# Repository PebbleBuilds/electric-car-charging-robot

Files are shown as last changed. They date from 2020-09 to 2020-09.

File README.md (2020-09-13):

# electric-car-charging-robot
This is a repo of files from an automatic electric car charging robot that I was designing with my friends Eddie Tian and Grace Wu before COVID19. This was done for a design course assignment with specific requirements, which are alluded to in our Project Proposal. 

For a summary of our plan, see Reports/Project Proposal.pdf. For a summary of the state of the robot as we left it before COVID19, see Reports/State of Robot as of March 2020.pdf. In the same file, there is also a list of the work breakdown between myself, Grace, and Eddie (I did not write all the files in this repo - I'm just uploading them here as a record of our work).

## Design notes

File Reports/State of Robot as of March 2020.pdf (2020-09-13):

Definitions:
The robot consists of three “stages” on which components are attached. The stage farthest from the test rig is the “x stage”, on the ground and closest to the test rig is the “y stage” and the highest stage is the “z stage.” Any components placed on these stages (such as motors and gears) will have a corresponding prefix. The end effector is attached to the z stage.

The lead screws which move the robot are named in the same fashion. The “x screw” is parallel to the test rig and the ground. The “y screw” is placed normal to the test rig. The “z screw” is parallel to the test rig and normal to the ground.

Our robot uses normal force carriers and platforms to transmit the rotational force of the gears into translational movement. When the gear turns and pushes the normal force carrier, it pushes the platform which is a block attached to the stage with an unthreaded screw which moves the stage in the desired direction. These components have the same prefix as the lead screw on which they move.

Robot Status
State of Mechanical
- Design of all mechanical components completed
- All components are finalized as of now except the following:
- The end effector has been assembled but not attached to the z stage.
- The camera mount has been assembled but not attached to the z stage.
- The top level of the robot the support rod holders attach to has been designed.
- The support rod holders has been designed.
- Motors have been placed in their respective mounts in the finalized position.
- Gears have been laser cut from acrylic and fitted to motors and lead screws.
- Movement along the x and y screws has been tested and functions on the ¾”-10 screws.
- X platform guard has been made to prevent wires from interfering with the x gears.
- Partial transition from ¾”-10 to ¾”-6 screws
- Note: due to supplier shortages, we were unable to use the lead screws specified in our design (¾”-6). Instead, we used ¾”-10 screws which we performed milestone 1 on
- After the milestone, we began to switch to ¾”-6 screws but still needs to be finished and tested.
Next steps:
- Finish transitioning to ¾”-6 screws.
- Laser cut the top level and support rod holders so support rods can be put in.
- Cut the polyethylene sheet to size so it can be attached to the z stage and slide along the support rods
- Test movement in the z direction
- Purchase standoffs to mount PCBs to stages
- Create guards around other moving parts to prevent harm to humans or wires.

- Determine if weight (sand or gravel) is required to weigh down the sides of the robot during operation.
Electrical
- Modular stepper motor driver circuits soldered (with pin headers for detaching/attaching drivers)
- Wire harness implemented for carrying power/signals between stages
- Circuits calibrated, debugged, and tested
Next steps:
- Add fan for active cooling, as well as 12V power from buck convertor for fan
- Design and purchase PCBs from Shenzhen to replace soldered perfboards, to increase current capacity and reliability (in time for Milestone 3)
- Remove excess solder from previously-used stepper motor drivers
- Address issues outlined in “Known Electrical Issues”

State of Software
- Raspberry Pi Zero W set up
- Flashed Raspberry Pi with Raspbian Stretch Lite
- Set up Raspberry Pi for headless SSH connection over mobile hotspot WiFi, laptop hotspot WiFi, and home WiFi
- Installed and updated ROS, OpenCV, and other necessary software onto Raspberry Pi
- Wrote Motor GPIO code to control 3 stepper motors, using commands received via ROS
- Wrote and tested a manual controller using PyGame and ROS to interface with Motor GPIO code
- Tested taking a picture with the Raspberry Pi’s attached camera and sending it to a laptop using SCP
- Performed an SSH ping test to find statistics on latency, upload rate, and download rate between laptop and Pi
- Camera set up and tested to obtain images
- OpenCV script written and tested to identify port indicators at a variety of angles
- Controls script written to derive speed and direction given CV output
- ROS elements integrated into CV and Controls code, testing required to validate
- Separate OpenCV and controls code, so that controls code can run at a different rate and make use of other sensor data as necessary (without need for multi-threading/multi-processing)
Next steps:
- Test OpenCV code for runtime on the Raspberry Pi and on a laptop
- Decide to run OpenCV code on Pi or on laptop based on findings
- If laptop is chosen, write shell script that sends images from the Pi to the laptop regularly via SCP, and find a way to have ROS messages move across devices
- Edit OpenCV code to read a continuous stream of pictures, and publish location data to other software elements via ROS
- Test software control loop with the rest of the robot in time for Milestone 2 - optimize for speed and precision in time for Milestone 3

Member Contributions
Eddie:
Mechanical Contributions:
- Created CAD of all components except gears and created an assembly of the robot
- Machined the platforms, adapters for gears to attach to the lead screws, laser cut the gears, laser cut the end effector at the Student Machine Shop
- Helped with construction of stages.
- Assembled the x screw end supports
- Assembled the robot with the help of Grace.
- Cut normal force carriers to size.
- Performed mechanical testing of the x and y stages
- Determined materials to be purchased at McMaster Carr and at Lowes
- Visited Lowes with Grace to pick up components (including a 6’ lead screw)
- Managed the change from ¾”-6 to ¾”-10 lead screws

Electrical Contributions:
- Soldered the wire harness
- Soldered the initial motor driver board without the headers
- Soldered the power supply board which houses the buck converter, the 5 V regulator, and the 3.3 V regulator.

Software Contributions:
- Helped select a suitable indicator for the computer vision software
- Helped determine which image processing tools are useful before indicator location is detected.
Grace:
Mechanical Contributions:
- Created CAD for Gears
- Constructed motor risers
- Helped with construction of stages
- Helped with construction for various other mechanical aspects (drilling, screws etc.)
- Constructed x-platform guard

Electrical Contributions:
- Soldered stepper motor driver circuit for one motor

Software Contributions:
- Designed port indicator setup and obtained images for testing purposes
- Implemented OpenCV to successfully detect port indicators from various different angles and orientations
- Created controls script informed by CV output
- Added ROS integrative elements to Controls and CV code

Rocco:

Mechanical Contributions:
- Helped design and construct end supports
- Helped make detailed design decisions such as:
- Size and orientation of stages
- Presence, thickness, and material for guiding rails
- Assembled robot to collect photo evidence

Electrical Contributions:
- Designed stepper motor driver circuits for 3 motors; soldered two of them onto perfboard
- Researched, tested, and calibrated buck converter and stepper motor drivers
- Selected and acquired interfacing components such as perfboards, wires, and pin headers based on requirements such as safety, current draw, and modularity
- Selected and acquired fan for active cooling
- Debugged circuits
- Helped design and implement wire harness

Software Contributions:
- Flashed Raspberry Pi with Raspbian Stretch Lite
- Set up Raspberry Pi for headless SSH connection over mobile hotspot WiFi, laptop hotspot WiFi, and home WiFi
- Installed and updated ROS, OpenCV, and other necessary software onto Raspberry Pi
- Wrote Motor GPIO code to control 3 stepper motors, using commands received via ROS
- Wrote and tested a manual controller using PyGame and ROS to interface with Motor GPIO code
- Tested taking a picture with the Raspberry Pi’s attached camera and sending it to a laptop using SCP
- Performed an SSH ping test to find statistics on latency, upload rate, and download rate between laptop and Pi

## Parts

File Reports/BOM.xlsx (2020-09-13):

Purchase Date | Source | Item | Quantity | Actual Price | Paid By | Status | Reported Price | Link to item (if applicable) | Tax column:
2020-01-29 | LFF | 1/4" plywood@$1.1/sqft | 3 | $3.30 | Eddie | Delivered | 3.3 |  | 0
2020-01-30 | StepperOnline | 5 Nema 17 2A stepper motors | 2020-02-05 | $15.86 | Eddie | Delivered | 15.86 |  | $2.06
2020-01-31 | BuyaPi | Camera | 1 | $13.00 | Rocco | Delivered | 12 | http://bit.ly/39VOazd | $1.69
2020-01-31 | BuyaPi | Raspberry Pi Zero W | 1 | $13.00 | Rocco | Delivered | 12 | http://bit.ly/32iQT37 | $1.69
2020-01-31 | BuyaPi | Mini Camera Cable | 1 | $5.00 | Rocco | Delivered | 5 | http://bit.ly/2HOGToS | $0.65
2020-01-31 | BuyaPi | BuyaPi Shipping | 1 | $11.00 | Rocco | Delivered | 11 |  | $1.43
2020-02-06 | McMaster Carr | Polyethylene Rod | 1 | $7.38 | Eddie | Delivered | 0 | https://www.mcmaster.com/ | 0
2020-02-06 | McMaster Carr | 1.5"*1.5"*1' steel bar | 1 | $32.23 | Eddie | Delivered | 32.23 | https://www.mcmaster.com/ | 0
2020-02-06 | McMaster Carr | 3/4-6 4' Lead Screw | 1 | $16.33 | Eddie | Delivered | 16.33 | https://www.mcmaster.com/ | 0
2020-02-06 | McMaster Carr | 3/4-6 3' Lead Screw | 1 | $12.73 | Eddie | Delivered | 0 | https://www.mcmaster.com/ | 0
2020-02-06 | McMaster Carr | 3/4-6 2' Lead Screw | 1 | $9.41 | Eddie | Delivered | 0 | https://www.mcmaster.com/ | 0
2020-02-06 | McMaster Carr | 2" diameter*3"long steel disc | 1 | $12.19 | Eddie | Delivered | 12.19 | https://www.mcmaster.com/ | 0
2020-02-06 | McMaster Carr | Polyethylene sheet | 1 | $3.81 | Eddie | Delivered | 0 | https://www.mcmaster.com/ | 0
2020-02-06 | McMaster Carr | Shipping/taxes | 1 | $77.35 | Eddie | Delivered | 41.33 | https://www.mcmaster.com/ | 0
2020-02-10 | LFF | Ball Caster | 2 | $4.44 | Eddie | Delivered | 4.44 | http://bit.ly/32gSkzj | 0
2020-02-10 | LFF | Wheel Coupling | 4 | $5.48 | Eddie | Delivered | 5.48 | https://bit.ly/3aI3C2S | 0
2020-02-10 | LFF | SG90 Servo | 1 | $1.50 | Eddie | Delivered | 1.5 | http://bit.ly/2SQMfGH | 0
2020-02-10 | LFF | Stepper Motor Driver | 1 | $1.83 | Eddie | Delivered | 1.83 | http://bit.ly/37Lvcd7 | 0
2020-02-10 | LFF | Female Barrel Plugs | 1 | $0.59 | Eddie | Delivered | 0.59 | http://bit.ly/2SSdmRD | 0
2020-02-10 | LFF | Workshop Rover | 1 | $99.22 | Eddie | Delivered | 0 |  | 0
2020-02-10 | LFF | Nema17 1.7A | 2 | $27.86 | Eddie | Delivered | 13.93 | http://bit.ly/2HL9s6H | 0
2020-02-10 | LFF | DCDC 3A Variable buck converter | 1 | $1.27 | Eddie | Delivered | 1.27 |  | 0
2020-02-12 | Amazon | Micro USB Male Plug | 1 | $0.87 | Eddie | Delivered | 0.87 | https://amzn.to/2SNusQx | $0.11
2020-02-12 | Amazon | 24V 6A Power Supply | 1 | $14.99 | Eddie | Delivered | 14.99 | https://amzn.to/3bYN7Al | $1.95
2020-02-19 | Lowes | Lead Screws - 5' | 1 | $33.33 | Eddie | Delivered | 0 | http://bit.ly/2vVbte0 | $4.33
2020-02-19 | Lowes | Lead Screws - 3' | 1 | $16.49 | Eddie | Delivered | 16.49 | http://bit.ly/2SQE1yo | $2.14
2020-02-19 | Lowes | Lead Screws - 2' | 1 | $13.49 | Eddie | Delivered | 13.49 | http://bit.ly/2uWaLwZ | $1.75
2020-02-19 | Lowes | Polyethylene Sliders | 1 | $3.79 | Eddie | Delivered | 1 | http://bit.ly/2SRzFGU | $0.49
2020-02-19 | Lowes | Washers | 1 | $3.99 | Eddie | Delivered | 0 | http://bit.ly/3bW7iPw | $0.52
2020-02-19 | Lowes | Pin | 1 | $1.49 | Eddie | Delivered | 0 | http://bit.ly/2T1DFUk | $0.19
2020-02-19 | Lowes | Nuts | 4 | $9.16 | Eddie | Delivered | 0 | http://bit.ly/2vRVqgV | $1.19
2020-02-19 | Amazon | Ball bearings | 2 | $10.52 | Eddie | Delivered | 0 | https://amzn.to/2Pin6T7 | $1.37
2020-02-20 | LFF | Gears (Laser Cut out of 3.58" squares) | 6 | $31.52 | Grace | Delivered | 5.64 | http://bit.ly/2PgYo5D | 0
2020-02-24 | LFF | 3D printed motor holder | 1 | $0.39 | Eddie | Delivered | 0 |  | 0
2020-02-24 | LFF | 3/4" ply@3.05/sqft | 2 | $6.10 | Eddie | Delivered | 6.1 |  | 0
2020-02-24 | LFF | 1/4" ply@1.22/sqft | 1 | $1.22 | Eddie | Delivered | 1.22 |  | 0
2020-02-24 | LFF | spruce 2*4@0.54/ft | 8 | $4.32 | Eddie | Delivered | 4.32 |  | 0
2020-03-03 | LFF | Tamiya Connectors | 2 | $1.20 | Eddie | Delivered | 1.2 | https://bit.ly/2JymghH | 0
2020-03-03 | LFF | Jumper Cable | 20 | $1.40 | Eddie | Delivered | 0 | https://bit.ly/3bYd7vd | 0
2020-03-04 | Home Hardware | Brown Perfboard | 2 | $6.00 | Rocco | Delivered | 0
2020-03-04 | Home Hardware | White Perfboard 3"x2" | 2 | $2.70 | Rocco | Delivered | 0
2020-03-04 | Home Hardware | 10 pin female header | 4 | $2.00 | Rocco | Delivered | 0
2020-03-04 | Home Hardware | Soldering wire | 1 | $2.69 | Rocco | Delivered | 0
2020-03-05 | LFF | Z-Stage (1/8" birch plywood - 5.5" x 5.5") | 0.2100694444 | $3.84 | Grace | Delivered | 3.84 | http://bit.ly/38PUdFn | 0
2020-03-06 | LFF | Tamiya Connectors | 6 | $3.60 | Grace | Delivered | 3.6 | https://bit.ly/2JymghH | 0
2020-03-07 | Home Hardware | Capacitors | 6 | $0.45 | Grace | Delivered | 1.35 |  | $0.06
2020-03-09 | Home Hardware | 80mm 12V 0.13A Case Fan | 1 | $9.99 | Rocco | Delivered | 0 |  | $1.30
2020-03-09 | Home Hardware | 20g Gorilla Glue | 1 | $8.69 | Rocco | Delivered | 0 |  | $1.13
2020-03-09 | Home Hardware | 8 pin male headers | 5 | $0.50 | Rocco | Delivered | 0 |  | $0.07
2020-03-09 | Home Hardware | Capacitors | 6 | $2.70 | Rocco | Delivered | 0 |  | $0.35
2020-03-10 | LFF | Protoboard | 1 | $1.04 | Eddie | Delivered | 1.04 | http://bit.ly/2Pjzy54 | 0
2020-03-10 | LFF | PVC Pipe | 8 | $5.36 | Eddie | Delivered | 0 |  | 0
 | LFF | Support rods | 4 | $3.00 | Grace | Delivered | 3 | http://bit.ly/2T9n6FR | 0
 | LFF | X-Stage (1/2" birch plywood - 13.5" x 5.5") | 0.515625 | $0.80 | Eddie | Delivered | 0.8 | http://bit.ly/38PUdFn | 0
 | LFF | Y-Stage (1/2" birch plywood - 12" x 5.5") | 0.4583333333 | $0.71 | Eddie | Delivered | 0.71 | http://bit.ly/38PUdFn | 0
 | Best Buy | 32GB MicroSD Card | 1 | $20.00 | Rocco | Delivered | 0 | http://bit.ly/3bVK0tf | $2.60
 | Taxes | Assuming 13%, LFF has no tax, McMaster Carr tax already with shipping |  | $7.04 |  |  | 0
Subtotal |  |  |  | $603.12 |  |  | 269.94 |  | 27.0803
Total with Tax |  |  |  | $610.16 |  |  | 297.0203
Partial Totals (no tax):
Eddie |  |  |  | $461.61
Grace |  |  |  | $42.41
Rocco |  |  |  | $97.27

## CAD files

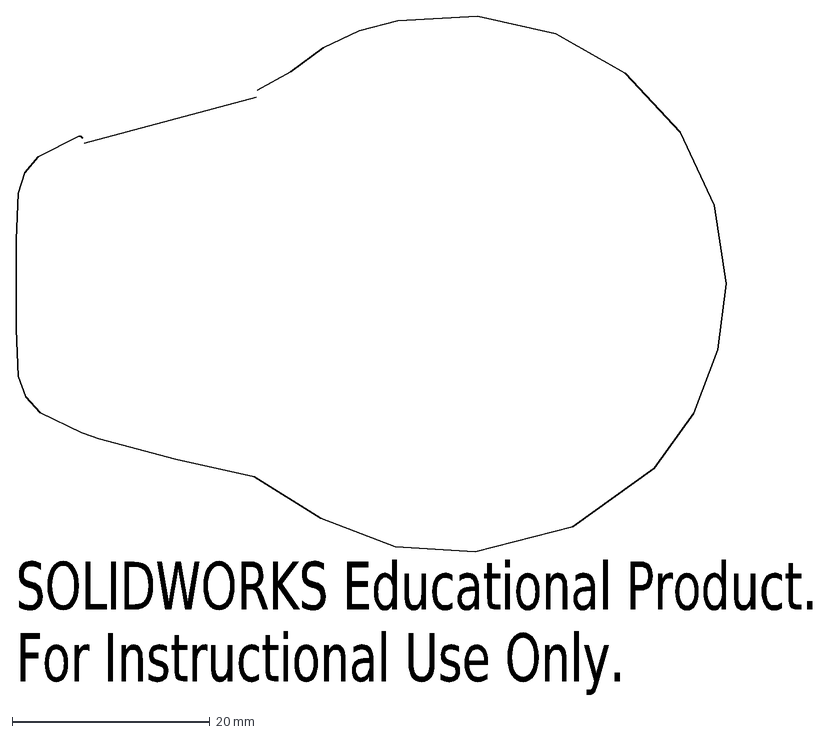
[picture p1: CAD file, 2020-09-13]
CAD Files/From Q/full clamp.DXF
SOLIDWORKS Educational Product.
For Instructional Use Only.

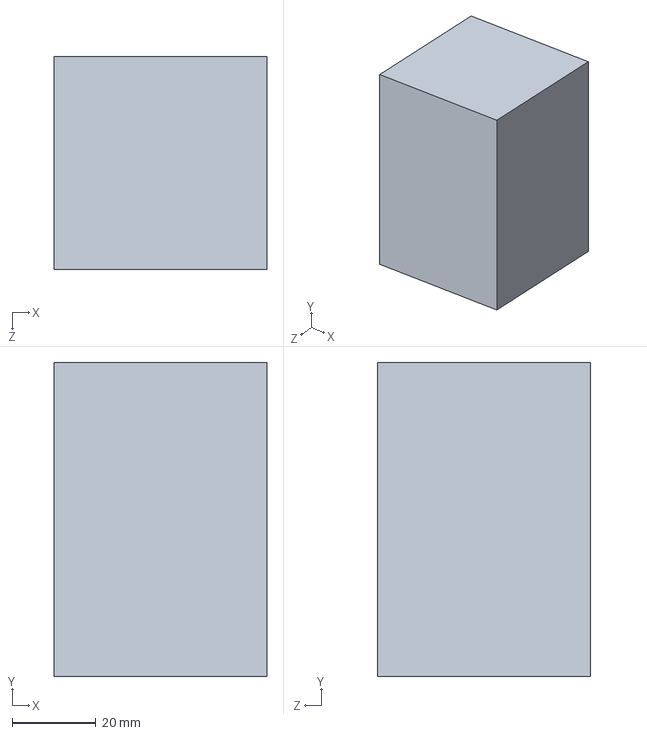
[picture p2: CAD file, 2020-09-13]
CAD Files/mystery caster ball and block assembly.SLDPRT
50.8 x 74.9 x 50.8 mm

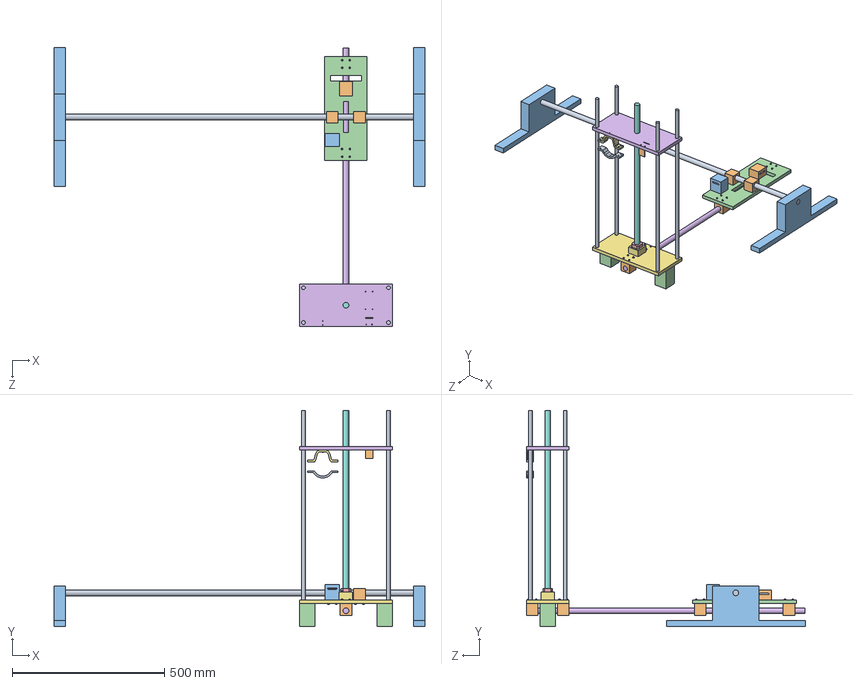
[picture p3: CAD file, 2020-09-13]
CAD Files/darover-nogearormotor.SLDASM
1219.2 x 709.9 x 916.3 mm
4'_lead
x-y-platform x 6
xendsupport x 2
x_stage
3Mx1.25in_screw x 24
3'_lead
y_stage
2'_lead
z_support_rod x 4
x-motor-riser
y-motor-riser
mystery caster ball and block assembly x 2
z_screw_holder
z-stage
clamp_top
3Mx0.5in_screw x 2
clamp_bottom
camera_mount

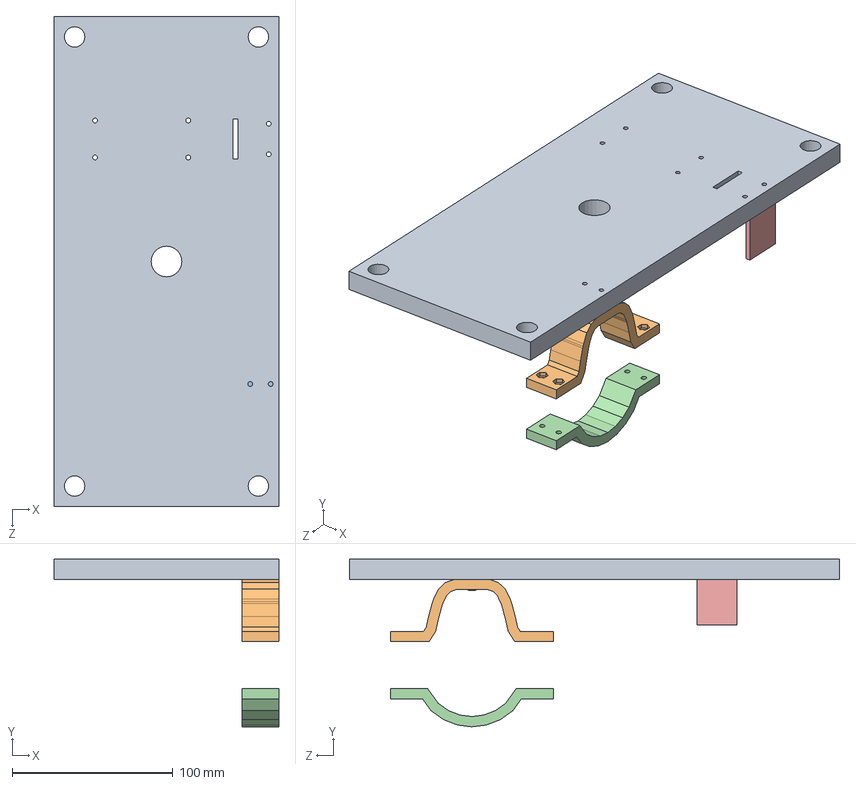
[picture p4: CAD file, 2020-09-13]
CAD Files/z-stage_assembly.SLDASM
139.7 x 104.3 x 304.8 mm
z-stage
clamp_top
3Mx0.5in_screw x 2
clamp_bottom
camera_mount

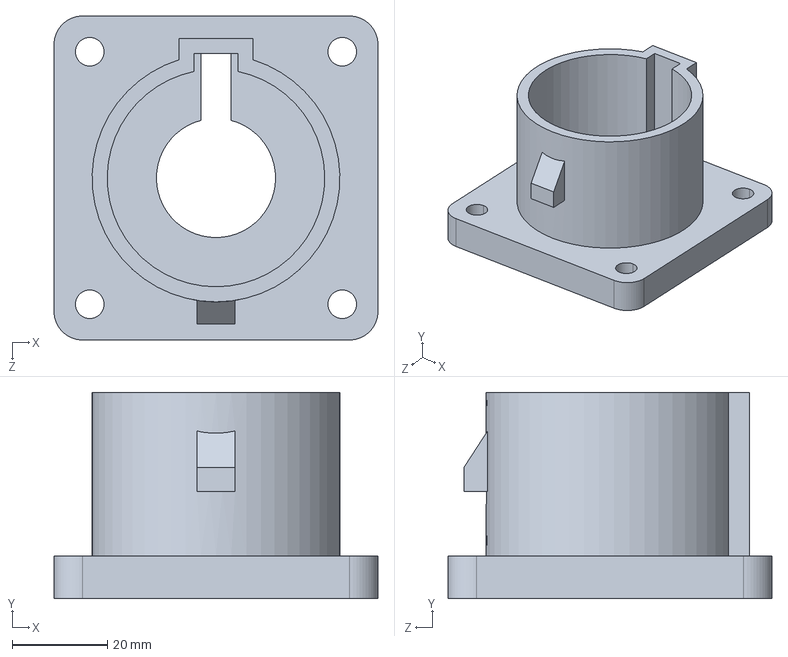
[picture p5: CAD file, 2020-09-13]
CAD Files/From Q/ChargePort3DP.STEP
68.0 x 43.3 x 68.0 mm

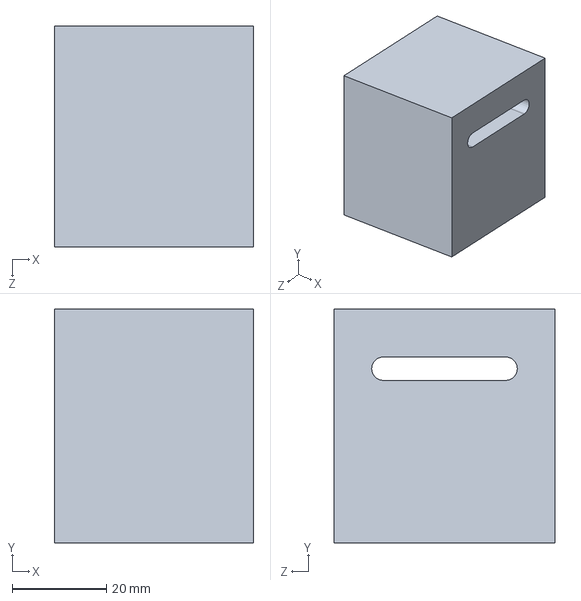
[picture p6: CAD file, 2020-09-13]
CAD Files/y-motor-riser.SLDPRT
42.4 x 49.8 x 47.0 mm

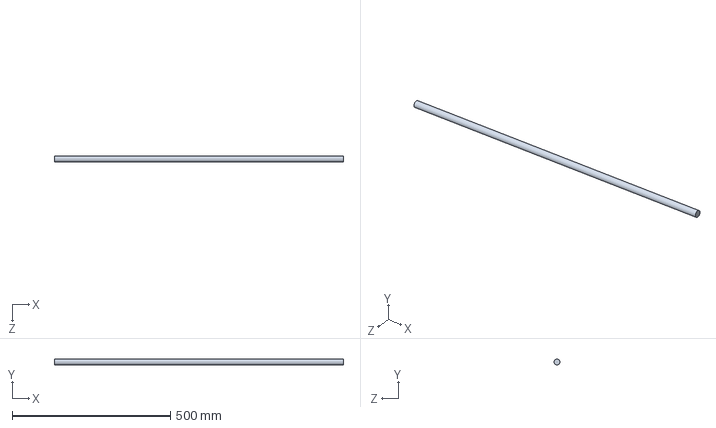
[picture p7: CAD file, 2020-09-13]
CAD Files/3__lead.SLDPRT
914.4 x 19.1 x 19.1 mm

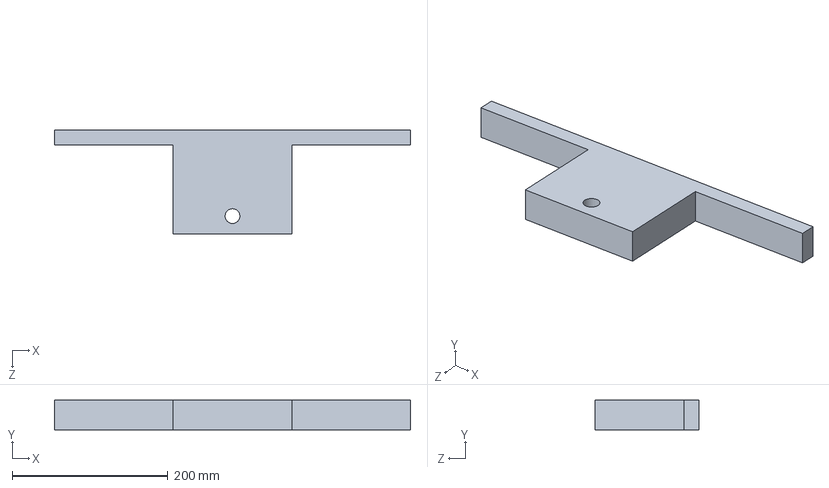
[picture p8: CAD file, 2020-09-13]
CAD Files/xendsupport.SLDPRT
457.2 x 38.1 x 133.4 mm

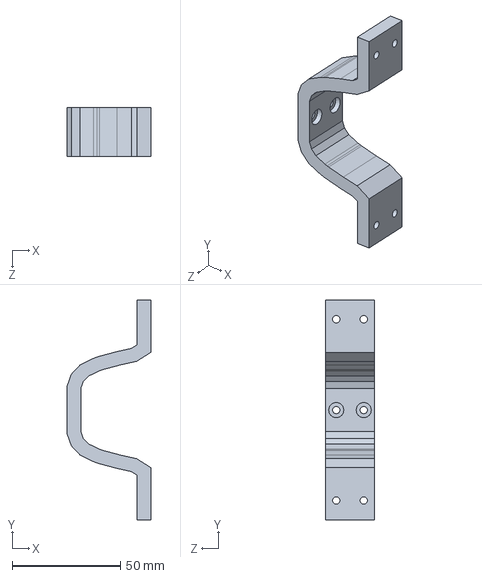
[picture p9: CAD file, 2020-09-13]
CAD Files/clamp_top.SLDPRT
38.6 x 101.6 x 22.9 mm

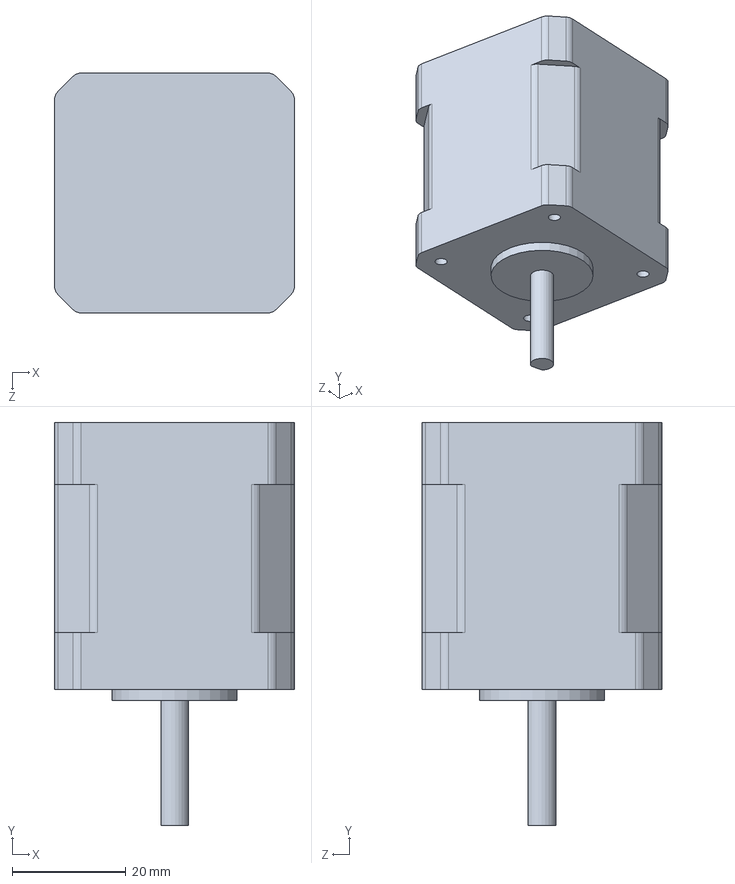
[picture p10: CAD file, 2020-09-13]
CAD Files/NEMA 17 Stepper Motor.SLDPRT
42.3 x 71.0 x 42.3 mm

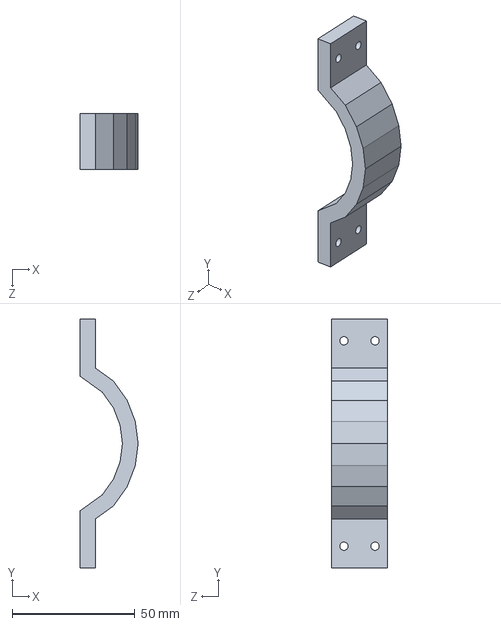
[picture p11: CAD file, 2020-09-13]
CAD Files/clamp_bottom.SLDPRT
23.8 x 101.6 x 22.9 mm

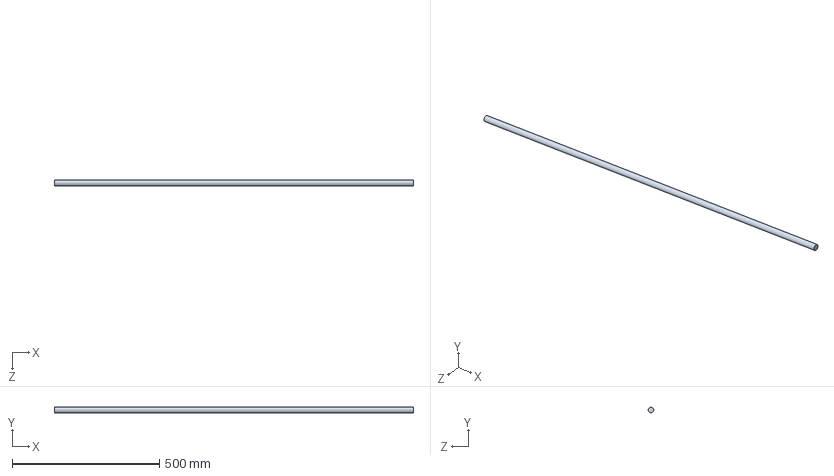
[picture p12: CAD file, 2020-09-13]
CAD Files/4__lead.SLDPRT
1219.2 x 19.1 x 19.1 mm

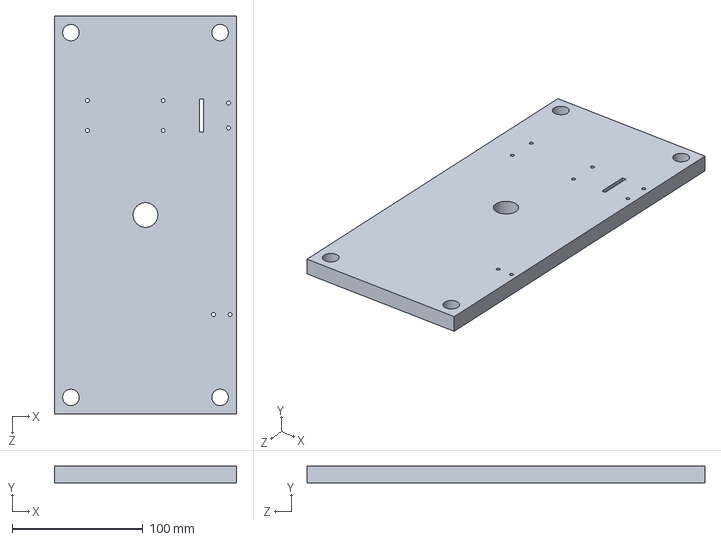
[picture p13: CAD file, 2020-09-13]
CAD Files/z-stage.SLDPRT
139.7 x 12.7 x 304.8 mm

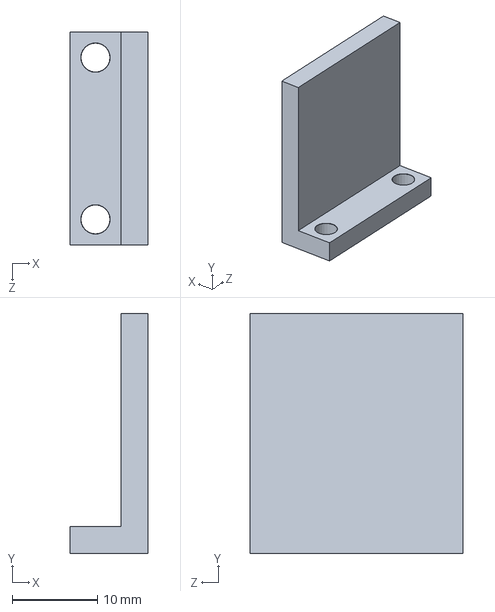
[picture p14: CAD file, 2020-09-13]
CAD Files/camera_mount.SLDPRT
9.18 x 28.2 x 25.0 mm

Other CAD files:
CAD Files/itsagear.SLDPRT
CAD Files/x-y-platform.SLDPRT
CAD Files/gearbuthex.SLDPRT
CAD Files/z-flange.SLDPRT
CAD Files/2__lead.SLDPRT
CAD Files/3Mx0.5in_screw.SLDPRT
CAD Files/3Mx1.25in_screw.SLDPRT
CAD Files/gear_adapter.SLDPRT
CAD Files/gearbuthex2.SLDPRT
CAD Files/itsagear2.SLDPRT
CAD Files/x-motor-riser.SLDPRT
CAD Files/x_stage.SLDPRT
CAD Files/y_stage.SLDPRT
CAD Files/z_screw_holder.SLDPRT
CAD Files/z_support_rod.SLDPRT

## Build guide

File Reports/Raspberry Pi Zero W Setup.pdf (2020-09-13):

ssh pi@raspberrypi.local

Usually people use NOOBS, which is an installer that Raspberry Pi runs and recommends. Decided against it, because:
- No monitor, keyboard, and mouse to control Pi with - thus, we need to set up with SSH.
- Want to make sure that we can get stuff we want on it (ROS, OpenCV)

Started following this tutorial for setting up a Pi Zero W with SSH: https://www.losant.com/blog/getting-started-with-the-raspberry-pi-zero-w-without-a-monitor

Happened to find a Raspbian Stretch Lite image with ROS Kinetic and OpenCV already installed, linked here:
https://discourse.ros.org/t/raspbian-stretch-lite-ros-opencv-raspberry-pi-disk-image/4294

Imaged it onto a 32GB MicroSD card, and continued following the tutorial to enable SSH

When creating wpa_supplicant.conf, changed a few key things:
- country from US to CAN (ISO code)
- WiFi network to my home wifi SSID and password
- This could be annoying later when doing UofT wifi - might want to hotspot for milestones or something
More info on wpa_supplicant.conf can be found here: https://www.raspberrypi-spy.co.uk/2017/04/manually-setting-up-pi-wifi-usingwpa_supplicant-conf/ (https://www.raspberrypi-spy.co.uk/2017/04/manually-setting-up-pi-wifi-using-wpa_supplicant-conf/)

Notable issue - because we were using the image from ROSbots, the password to SSH into the Pi was no longer “raspberry” as is the default - it was instead “rosbots!”

Once I got into the Pi, I stopped following the old tutorial and started following this one, specific to this image: https://github.com/ROSbots/rosbots_setup_tools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 (https://github.com/ROSbots/rosbots_setup_tools)

I changed the UNIX password on our Pi to “M19”

At this point I decided it would be a good idea to pull out the plug for the Pi - this is a bad idea. Every time you turn it off, you need to run:

sudo shutdown -h now
Plugged back in to check everything is okay. Got this error:

@@@@@@@@@@@@@@@@@@@@@@@@@@@@@@@@@@@@@@@@ @@@@@@@@@@@@@@@@@@@
@ | WARNING: POSSIBLE DNS SPOOFING DETECTED! | @
@@@@@@@@@@@@@@@@@@@@@@@@@@@@@@@@@@@@@@@@ @@@@@@@@@@@@@@@@@@@
The ECDSA host key for raspberrypi.local has changed, and the key for the corresponding IP address 192.168.0.24 is unknown. This could either mean that
DNS SPOOFING is happening or the IP address for the host
and its host key have changed at the same time. @@@@@@@@@@@@@@@@@@@@@@@@@@@@@@@@@@@@@@@@ @@@@@@@@@@@@@@@@@@@
@ WARNING: REMOTE HOST IDENTIFICATION HAS CHANGED! @ @@@@@@@@@@@@@@@@@@@@@@@@@@@@@@@@@@@@@@@@ @@@@@@@@@@@@@@@@@@@
IT IS POSSIBLE THAT SOMEONE IS DOING SOMETHING NASTY!
Someone could be eavesdropping on you right now (man-in-the-middle attack)!
It is also possible that a host key has just been changed.
The fingerprint for the ECDSA key sent by the remote host is SHA256:tSo0taYd+ODfsEIJray7eqDhH9jRNc4re+3TgvqWc7o.
Please contact your system administrator.
Add correct host key in C:\\Users\\bluey/.ssh/known_hosts to get rid of this message

Probably because we changed the device settings earlier - to amend this, I went to C:\\Users\\bluey/.ssh/known_hosts and deleted all known hosts, to try again.

After doing so, I was able to SSH in as normal, with password “M19”

Writing Motor GPIO code for the Pi
Using this tutorial:
https://www.raspberrypi.org/documentation/usage/gpio/python/README.md

Made a directory, ~/robot, that we’ll put all our future code into

We want to control the GPIO pins from our computer, so we’ll install the GPIO Zero library on Rocco’s computer and use the Remote GPIO feature.

Accidentally sudo apt updated the Pi and command killed it right after. Hopefully didnt break anything. If anything, run sudo apt update on Pi maybe? Or re-flash

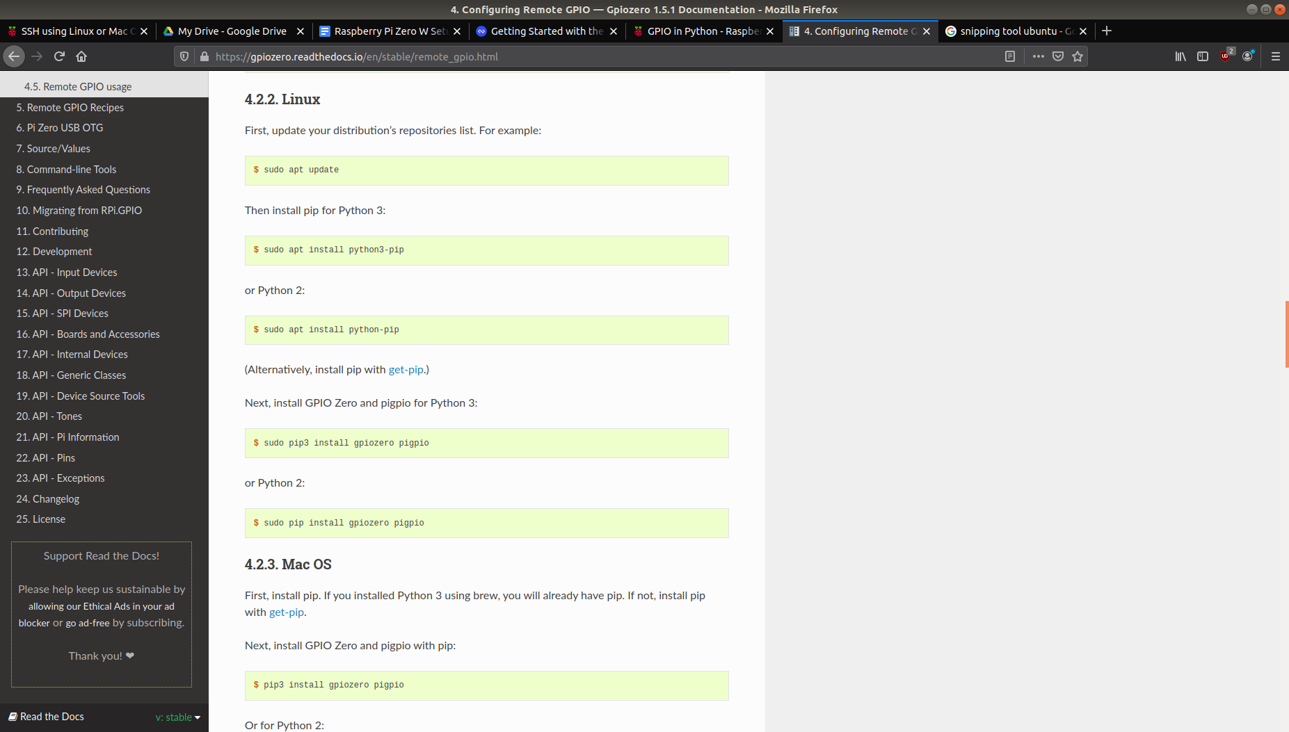
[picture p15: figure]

We:
- Installed pigpio and gpiozero on my laptop
- Installed pigpio on the pi

We then realized that we would have to set a static IP address on the Pi if we wanted to be able to set the environment variable without checking for the IP of the Pi every single time

But I got scared so we’ll do that later as a stretch goal

Okay - we’re gonna have to make the motor GPIO code in a catkin_ws so we can mess with it later

So I created and built a ROS package called M19 using this tutorial http://wiki.ros.org/ROS/Tutorials/CreatingPackage

And I need to write a manual controller (publisher), and something that does remote GPIO to the Pi (subscriber)

NOTE: If we ever try to use roslaunch, note that the subscriber with gpiozero has to be run with a command that also initializes an environment variable with the IP of the Pi, as noted above

For publisher:
- using code from this forum https://ubuntuforums.org/showthread.php?t=2394609 to read keypresses
- can’t read multiple keypresses at once this way - could fix this using pygame

At the end of Friday, February 14th:
- publisher runs and publishes, but does not respond to button presses

- subscriber untested, probably wont run because of variables out of scope
- subscriber uses spinOnce(), which is a cool thing
- and uses a while loop while modding a timer to control the driver pulses
- cool!
- please work

February 16, 2020
- Took the Pi to Markham home, tried to do the wpa_supplicant.conf file thing to change the settings
- turns out you can only do it with an SD card that has never been booted
- so if I want to do it again I need to re-flash the SD card
- hmm
- so far, all I’ve done is change some settings to enable camera and Remote GPIO
■ re-flashing should be okay - I plan to be home for a couple days so may as well
- https://www.daemon-systems.org/man/wpa_supplicant.conf.5.html (wpa_supplicant params)
- not working - going to reflash again

March 2nd
- Got Pi to work on my own hotspot
- RPZW doesnt work on 5GHz
- New password - orangecheesecake
- Check wireshark (sudo wireshark) for Pi IP (10.42.0.209)
- Re ran through rosbots setup, re-enabled remote gpio

March 4th
- Pi is being powered via GPIO - just dont use the pi to output power
- Having issues with pi connecting to my computer, but not to the internet
- https://docs.ubuntu.com/core/en/stacks/network/wifi-ap/docs/simultaneoussta-ap-mode (https://docs.ubuntu.com/core/en/stacks/network/wifi-ap/docs/simultaneous-sta-ap-mode) following this tutorial to change my wifi configurations to get it to work
- tried to also create a virtual environment to swap between python 2 and 3 with this https://stackoverflow.com/questions/42214414/this-package-shouldnot-be-accessible-on-python-3-when-running-python3 (https://stackoverflow.com/questions/42214414/this-package-should-not-be-accessible-on-python-3-when-running-python3)
- source env/bin/activate to activate python3 mode
■ made an alias: python3mode
- deactivate to leave
- python --version to check which one you’re on
- https://unix.stackexchange.com/questions/84440/hotspot-and-internet-accesstogether-why-not (https://unix.stackexchange.com/questions/84440/hotspot-and-internet-access-together-why-not) ACTUAL tutorial for wifi hotspot setup
- uses create-ap package from github
- made an alias on my computer - just type “hotspot” for hotspot
- For my weird python path problem, this is why:
- https://answers.ros.org/question/310401/ros-changed-the-python-path/

- ROS Melodic automagically changes my python path to 2.7 upon calling setup.bash. So I shouldn’t do this automatically on startup - instead I’ll make an alias that does it
- Made the alias - called rossetup

March 8th
- When my laptop hotspot opens, it closes connection with UofT wifi (no internet)
- Workaround - create a virtual access point (with create_ap)
■ Problem - virtual access point is at 5GHz
- Mobile hotspot works, but has WPA2/AES protocol
- Need the following lines in wpa_supplicant:
■ proto=RSN
■ key_mgmt=WPA-PSK
■ pairwise=CCMP
■ auth_alg=OPEN
- installing tmux onto Pi for screen splitting
- installed

March 10th
- Camera responds to command raspistill -o image.jpg for taking pictures
- image saved as image.jpg on my current working directory
- sudo apt-get update returning an error about missing pub_key
- image successfully moved to desktop and opened
- pretty nice pic
- needed to install openssh https://www.cyberciti.biz/faq/ubuntu-linux-installopenssh-server/ (https://www.cyberciti.biz/faq/ubuntu-linux-install-openssh-server/)
- and run 2 commands - ill probably add em to my bashrc
■ the commands enabled and started my computer’s SSH
- took 7-8 secs to take a pic
- could probably be cut down with settings at the expense of quality
- could also take video - raspistill supports it
- installing sshping on my computer to try to diagnose latency of ssh connection
- its really slow typing in commands
- tool i’ve been using: Nmap
- type nmap -sn (network interface name - for example, wlp2s0) (ip address, but with the last set of numbers replaced with a star)
- okay - installed sshping, ran it with the pi (ON MY HOME WIFI)
- these are the results
■ ssh-Login-Time: | 5347254262 ns
■ Minimum-Latency: | 4023370 ns
■ Median-Latency: | 4785313 ns
■ Average-Latency: | 6181728 ns
■ Average-Deviation: 13950283 ns
■ Maximum-Latency: | 234363761 ns
■ Echo-Count: | 1000 B
■ Upload-Size: | 8000000 B
■ Upload-Rate: | 2269879 B/s
■ Download-Size: | 8000000 B

■ Download-Rate: 1644790 B/s
- that looks good! around 4 ping
■ maximum ping 234 ms
- why is it so slow typing stuff >.>
- upload rate 2.2 MBps, download rate 1.6 MBps
- my image was 2.5 MB, o that’s 1.5625 seconds to send an image
- Grace meeting notes
- How to get pictures?
■ Either OpenCV will run on Pi or on laptop
- If on Pi, run shell command to take pics regularly, and OpenCV will take the newest pic every time
- If on laptop, same thing, but Rocco will have to write a shell script to get everything over via SCP on a regular basis
- Should OpenCV and controls be separate?
■ Currently, it doesn’t matter, because OpenCV is the only feedback to our loop, so motors only need to be updated every time OpenCV finishes a picture
■ Later, we might decide to add other sensors that need to be polled faster. If so, controls should run separately. Look into multithreading/multiprocessing if necessary, but ROS should make this okeydoke
- Example/ we have a button and OpenCV coords
- we’ll ros spinOnce every time we poll the button and so we’ll get updated camera stuff if its there
■ Conclusion: yes we will make them separate
- How does delay in image transfer affect delays in controls response? ■ We don’t know :((( read stuff i guess
- To do (Rocco):
- Run sshping on hotspot
- Compile and test motor code
■ Find min and max motor values
■ Remember to adjust VREF if you change VDD
- Try to run OpenCV code on Pi, and time it
■ Decide whether to run on Pi or laptop
- If laptop:
■ Write shell script for SCP to laptop
■ Figure out how to get ROS messages from OpenCV/control node on laptop to control/motor node on Pi
- Separate OpenCV and control code
- Eventually, write an alias that will start everything at once

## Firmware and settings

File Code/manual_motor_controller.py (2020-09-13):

#!/usr/bin/env python
# license removed for brevity
import rospy
from std_msgs.msg import String

import sys, termios, tty, os, time, fcntl, pygame
from pygame.locals import *

def talker():
    pygame.init()
    screen = pygame.display.set_mode((640,480))
    clock = pygame.time.Clock()
    x_dir = "stop"
    y_dir = "stop"
    z_dir = "stop"
    x_speed = 0
    y_speed = 0
    z_speed = 0
    pub = rospy.Publisher('motor_commands', String, queue_size=10)
    rospy.init_node('manual_motor_controller', anonymous=False)
    rate = rospy.Rate(10) # 10hz
    while not rospy.is_shutdown():
        pygame.event.pump()
        keys=pygame.key.get_pressed()
        print(keys[K_a])
        if (keys[K_a]):
            x_dir = "left"
        elif (keys[K_d]):
            x_dir = "right"
        else:
            x_dir = "stop"
        if (keys[K_w]):
            y_dir = "forward"
        elif (keys[K_s]):
            y_dir = "back"
        else:
            y_dir = "stop"
        if (keys[K_i]):
            z_dir = "up"
        elif (keys[K_k]):
            z_dir = "down"
        else:
            z_dir = "stop"
        if (keys[K_l]):
            x_speed += 100
            y_speed += 100
            z_speed += 100
        elif (keys[K_j]):
            x_speed -= 100
            y_speed -= 100
            z_speed -= 100
        if (x_speed > 10000):
            x_speed = 10000
        elif (x_speed < 0):
            x_speed = 0
        if (y_speed > 10000):
            y_speed = 10000
        elif (y_speed < 0):
            y_speed = 0
        if (z_speed > 10000):
            z_speed = 10000
        elif (z_speed < 0):
            z_speed = 0
        commands = x_dir+" "+str(x_speed)+" "+y_dir+" "+str(y_speed)+" "+z_dir+" "+str(z_speed)
        print(commands)
        rospy.loginfo(commands)
        pub.publish(commands)
        rate.sleep()

if __name__ == '__main__':
    try:
        talker()
    except rospy.ROSInterruptException:
        pass

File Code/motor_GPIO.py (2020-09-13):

#!/usr/bin/env python
import rospy, gpiozero, time
from std_msgs.msg import String

commands = ["left",0,"back",0,"up",0]

def callback(data):
    rospy.loginfo(rospy.get_caller_id() + "I heard %s", data.data)
    global commands=(data.data).split()
    global commands[2]=int(commands[2])
    global commands[4]=int(commands[4])
    global commands[6]=int(commands[6])

def listener():

    # In ROS, nodes are uniquely named. If two nodes with the same
    # name are launched, the previous one is kicked off. The
    # anonymous=True flag means that rospy will choose a unique
    # name for our 'listener' node so that multiple listeners can
    # run simultaneously.
    rospy.init_node('motor_GPIO', anonymous=False)

    rospy.Subscriber("motor_commands", String, callback)
    x_dirPin = gpiozero.LED(2)
    y_dirPin = gpiozero.LED(4)
    z_dirPin = gpiozero.LED(6)
    x_speedPin = gpiozero.LED(3)
    y_speedPin = gpiozero.LED(5)
    z_speedPin = gpiozero.LED(7)


    while not rospy.is_shutdown():
#directional pins
        if (commands[0] == "left"):
            x_dirPin.off()
        else:
            x_dirPin.on()
        if (commands[2] == "back"):
            y_dirPin.off()
        else:
            y_dirPin.on()
        if (commands[4] == "down"):
            z_dirPin.off()
        else:
            z_dirPin.on()

#update speeds
        x_speed = int(commands[1])
        y_speed = int(commands[3])
        z_speed = int(commands[5])

#if you're not holding down the button, set speed to zero
        if (commands[0] == "stop"):
            x_speed = 0
        if (commands[2] == "stop"):
            y_speed = 0
        if (commands[4] == "stop"):
            z_speed = 0

#finds periods at which to pulse with
        x_period = 1/x_speed*1000000
        y_period = 1/y_speed*1000000
        z_period = 1/z_speed*1000000

#use mod of timer by period to see if it's time to pulse on or off
        if((time.time*1000000)%x_period < x_period//2):
            x_speedPin.on()
        else:
            x_speedPin.off()
        if((time.time*1000000)%y_period < y_period//2):
            y_speedPin.on()
        else:
            x_speedPin.off()
        if((time.time*1000000)%z_period < z_period//2):
            z_speedPin.on()
        else:
            z_speedPin.off()
        rospy.spinOnce() # spinOnce() checks for new messages once
        
#end of while loop

if __name__ == '__main__':
    listener()

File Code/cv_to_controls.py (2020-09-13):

def controls(circle, axis):
    speed = None
    if axis == 'x':
        if circle[0] > resizedw/3 and circle[0] < 2*resizedw/3:
            if circle[0] < resizedw/2 + 5 and circle[0] > resizedw/2 - 5:
                speed = 'stop'
            else:
                speed = 'slow'
        else: 
            speed = "fast"
    elif axis == 'z':
        if circle[1] > resizedh/3 and circle[1] < 2*resizedh/3:
            if circle[1] < resizedh/2 + 5 and circle[1] > resizedh/2 - 5:
                speed = 'stop'
            else:
                speed = 'slow'
        else: 
            speed = "fast"
    elif axis == 'y':
        if circle[2] > slowrad:
            if circle[2] > stoprad:
                speed = 'stop'
            else:
                speed = "slow"
        else:
            speed = 'fast'
    return speed
